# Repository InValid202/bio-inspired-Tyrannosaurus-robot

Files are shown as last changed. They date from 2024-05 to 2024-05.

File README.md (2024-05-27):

# Bio-inspired-Tyrannosaurus-robot
Dinosaur project for RE60429
## Feature
### Robot

Front view

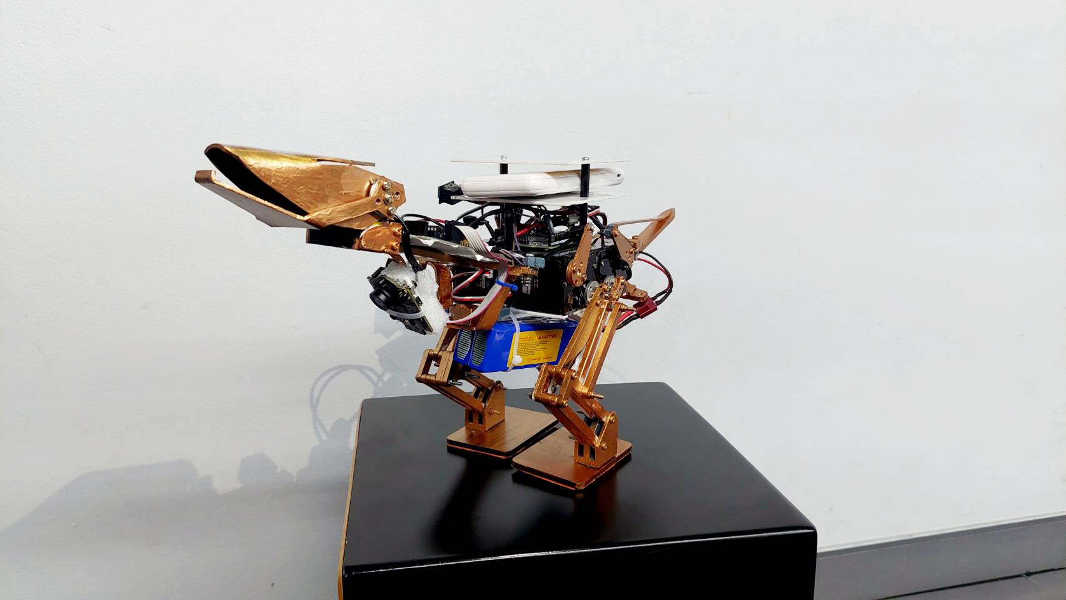
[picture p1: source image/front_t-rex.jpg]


Side view

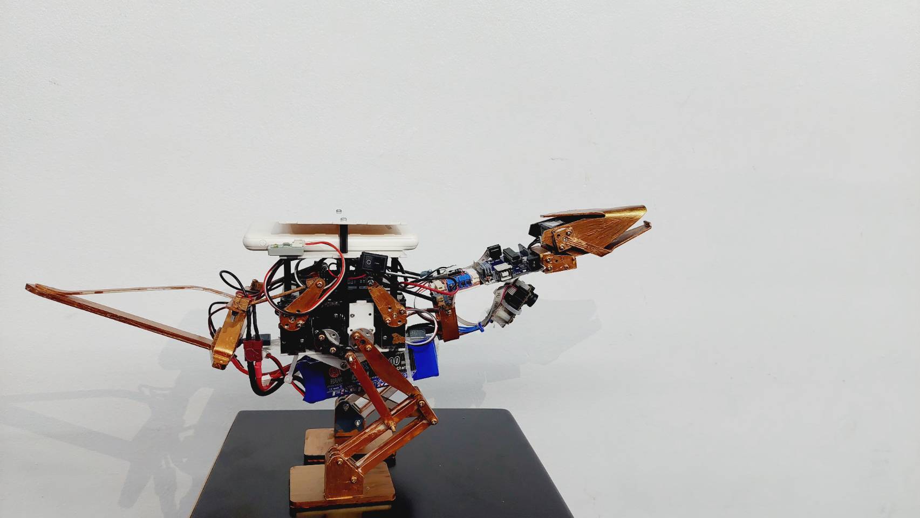
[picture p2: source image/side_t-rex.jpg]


Bird's eye view

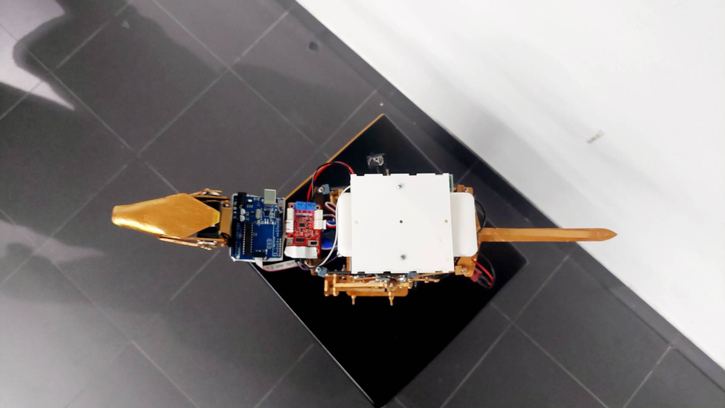
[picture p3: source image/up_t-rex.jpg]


### T-REX's food

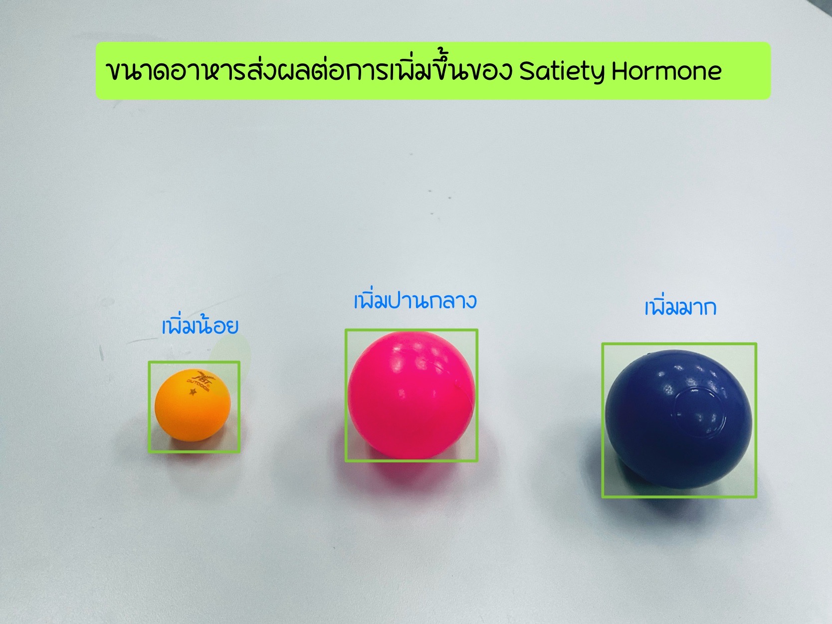
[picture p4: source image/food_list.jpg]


### T-REX's life cycle


## Theory
### CPG with VRNs

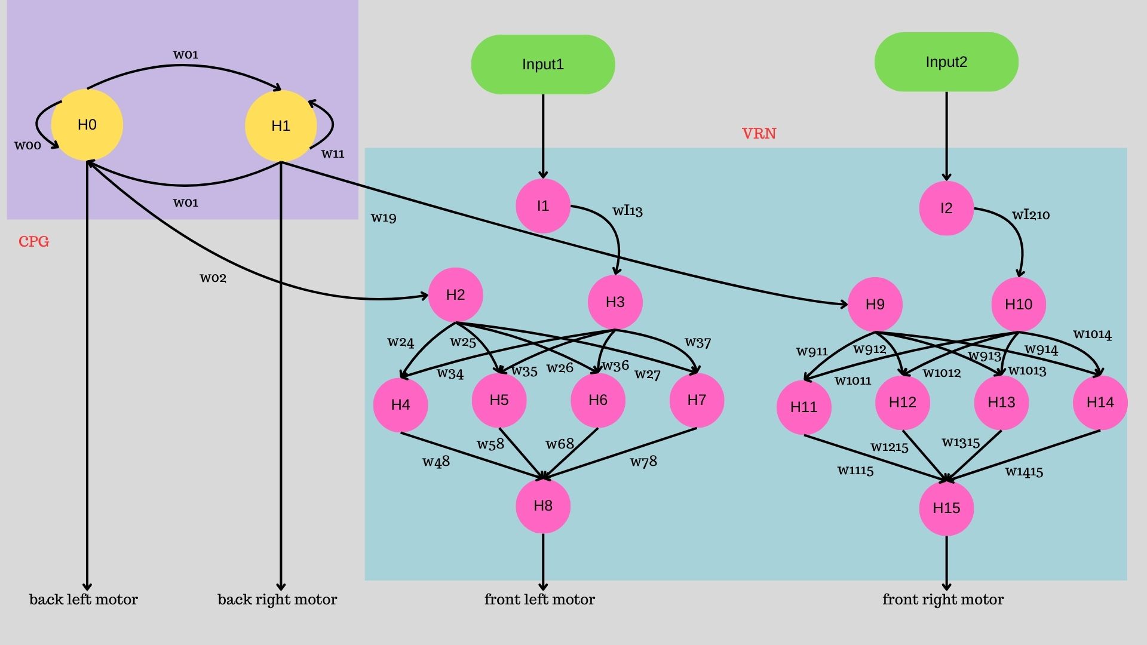
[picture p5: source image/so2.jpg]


spreadsheets for represent CPG and VRNs: [https://docs.google.com/spreadsheets/d/1AZzXm8qZo_j3j6RvV-UtCaSccyqd9fPiu6YYuq5pqpM/edit#gid=0](https://docs.google.com/spreadsheets/d/1AZzXm8qZo_j3j6RvV-UtCaSccyqd9fPiu6YYuq5pqpM/edit?usp=sharing)

as you can see in the spreadsheets you will see a output from both VRNs will always shift a little bit early than original output of SO2 so i assign each VRNs output for each side to the front motor that has responsibility to lift up a leg and assign back motor with output from CPG, this config will generate a pattern of walking by lift up a leg with front motor and follow by stretch leg back with back motor. and other good thing about using VRNs that i can adjust input to modify amplitude of VRNs output. so, i can make my robot turn left and turn right. for example, if i want to turn left i can lower my input1 to make O8 amplitude get lower and will result in lower lifting range but right side still has the same lifting range as before, my robot will start to turn left by it own. 

### Hormone

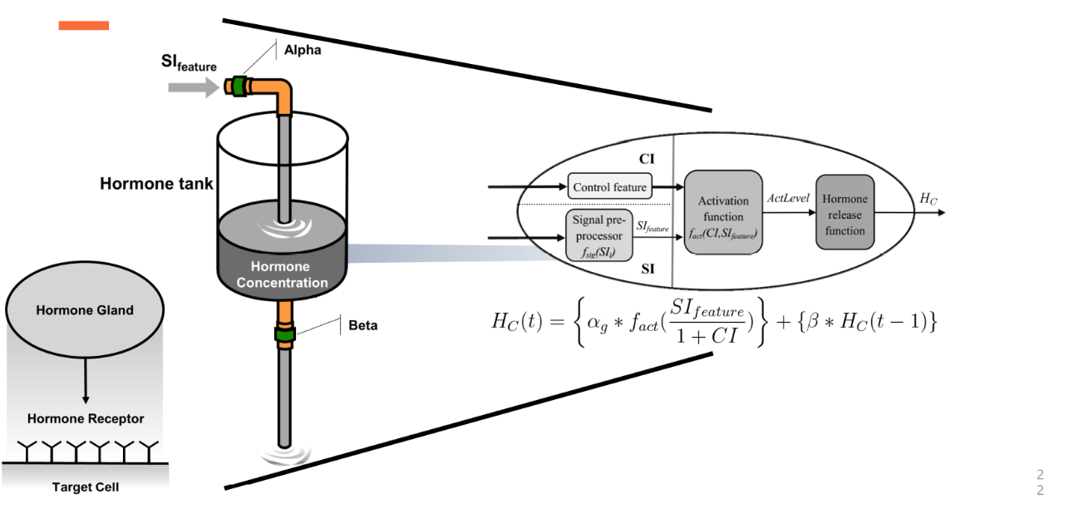
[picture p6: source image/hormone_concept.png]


Example spreadsheets for represent artificial hormones: https://docs.google.com/spreadsheets/d/1hGDivs0pLVSncBLwVF0gHtu8sqr4KoLUj5qkTngY2NQ/edit?usp=sharing

addition paper: [FIBO205_240514_210108.pdf](https://github.com/InValid202/bio-inspired-Tyrannosaurus-robot/files/15449666/FIBO205_240514_210108.pdf)

### System diagram

core concept of this system diagram was to use a Arduino UNO R4 handle all low level control such as drive motor or maybe control a buzzer follow by message from ROS node, and use other ros node handle all high level control such as hormone system calculation and CPG with VRNs

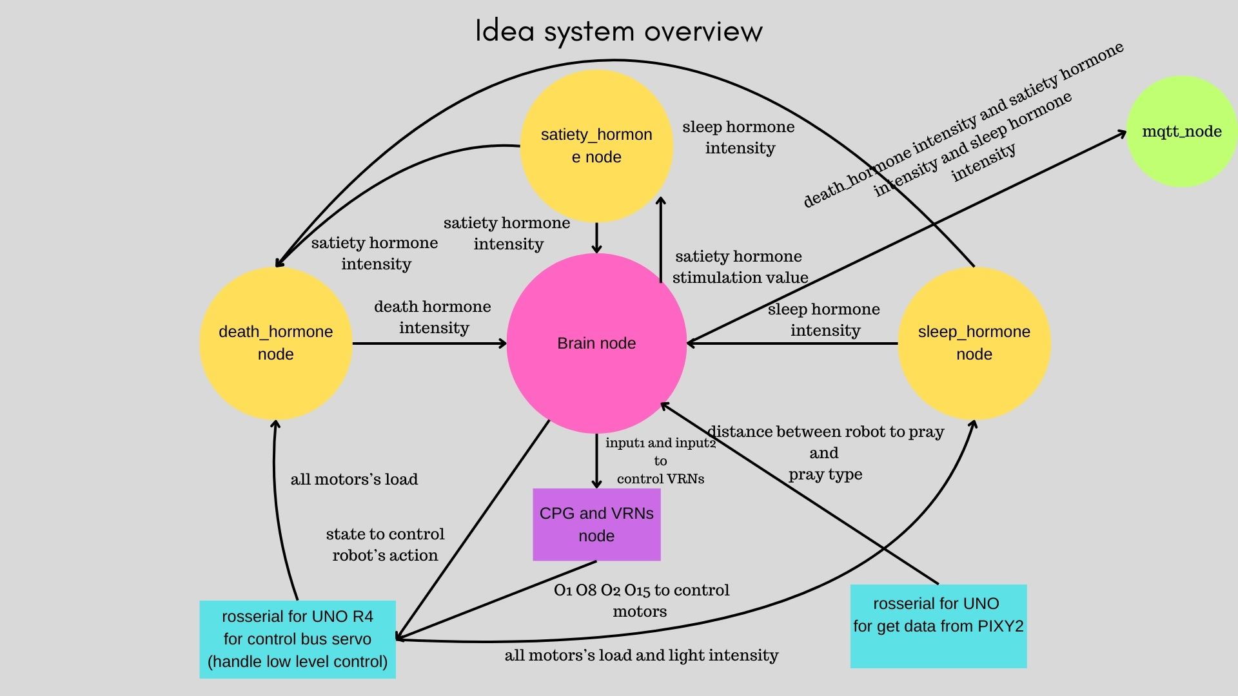
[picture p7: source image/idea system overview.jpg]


After trying to use this system diagram as the core concept for programming, I found that rosserial on the Arduino UNO R4 couldn't handle a message from the ROS CPG node. So, I integrated the following nodes together in the Arduino UNO R4 and ended up with this diagram:

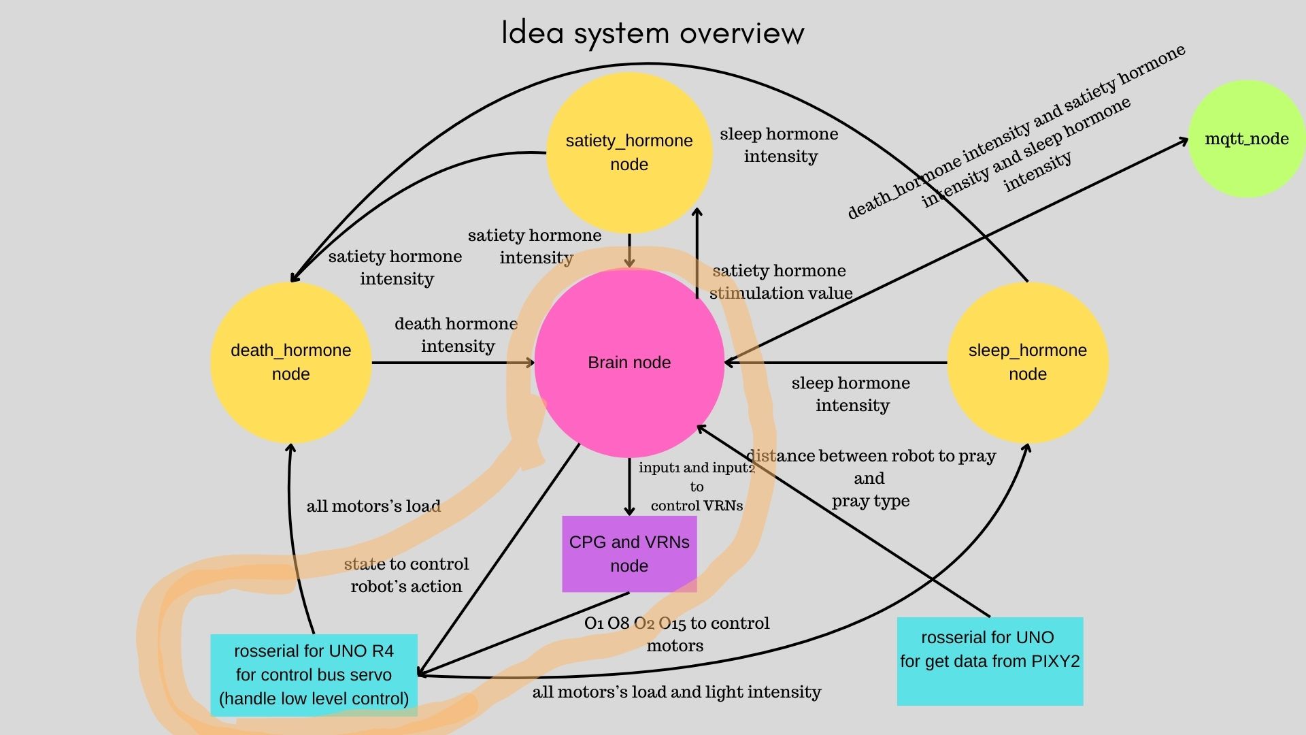
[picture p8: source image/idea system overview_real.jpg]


### Distance calculation Between an Object and a Camera
#### Equation for Finding the Distance Between an Object
and a Camera

𝐷 = 𝑘 / d

Where:

• 𝐷 is the size of the object in the image

• 𝑑 is the distance between the camera and the object

• 𝑘 is a constant that needs to be determined from the actual size of the object

#### Finding the Constant 𝑘
If you know the actual size of the object ( 𝑆 ), you can use the following relationship to
find the constant 𝑘 :

𝑘 = 𝐷 * 𝑑

However, since we do not have the distance ( 𝑑 ) and the diameter in the image ( 𝐷 ), we
need to use the actual size of the object ( 𝑆 ) as a basis to create a general equation.
Suppose you have the actual size of the object 𝑆 = 40 mm.

#### Creating the General Equation
We know that the size of the object in the image ( 𝐷 ) is inversely proportional to the
distance ( 𝑑 ), with a constant 𝑘 that is related to the actual size of the object 𝑆 :

𝑘 = 𝑆 * 𝑑

Thus, the equation becomes:

𝐷 = 𝑘 / d

When 𝑘 = 𝑆 * 𝑑

#### Summary of the Equation

𝐷 = (𝑆 * 𝑑) / 𝑑 = 𝑆

If you know the actual size of the object and the size in the image, you can find the
distance:

𝑑 = 𝑘 / 𝐷

If the constant 𝑘k is not known, you need to know the size of the object in the image
for a given distance or know the focal length of the camera to establish this relationship.

#### Example Usage

Suppose you know the actual size of the object 𝑆=40 mm. and the size of the object in
the image 𝐷 :

If you know that the size of the object in the image at a distance 𝑑 = 10 cm. is 𝐷 = 100
mm. :

1. Find the constant 𝑘 :
𝑘 = 𝐷 * 𝑑 = 100 * 10 = 1000
2. Use the general equation:
𝐷 = 1000 * 𝑑
3. If the size of the object in the image 𝐷D is 50 mm and you want to find 𝑑d :
𝑑 = 1000 / 50 = 20 cm.

This equation can be used when you know the actual size of the object and have
information about the size of the object in the image or the distance in one case to find
the constant 𝑘 first.

## installation

### Hardware:

#### Requirement:

1. Arduino Uno R4 WiFi

2. Arduino Uno R3 

3. Feetech SCS SERVO CONTROLLER

4. Jetson nano

5. Servo scs15

6. pixy2.1
   
7. ZX-02F Light sensor

8. PowerBank 5 V 2A

9. LiPO Battery 3000mAh

10. Rocker switch ON-OFF

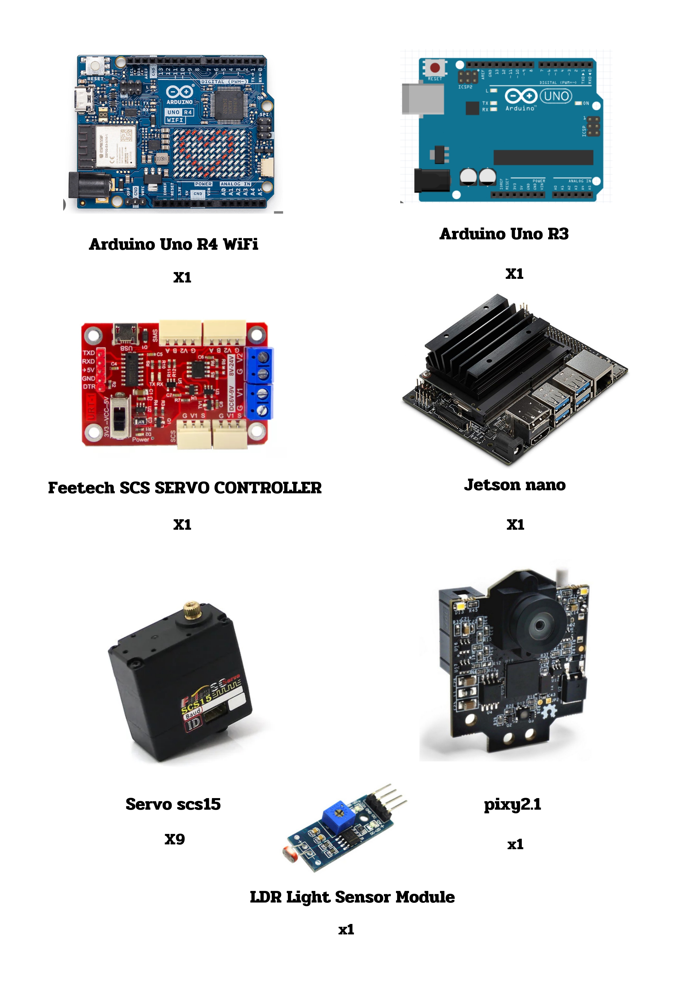
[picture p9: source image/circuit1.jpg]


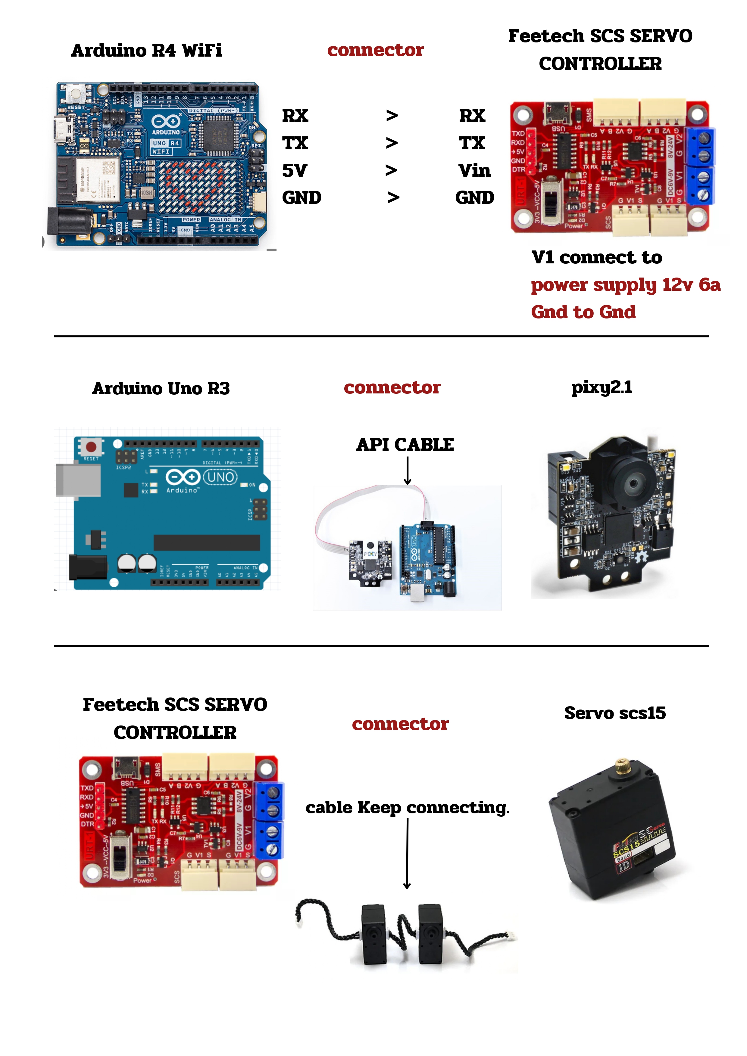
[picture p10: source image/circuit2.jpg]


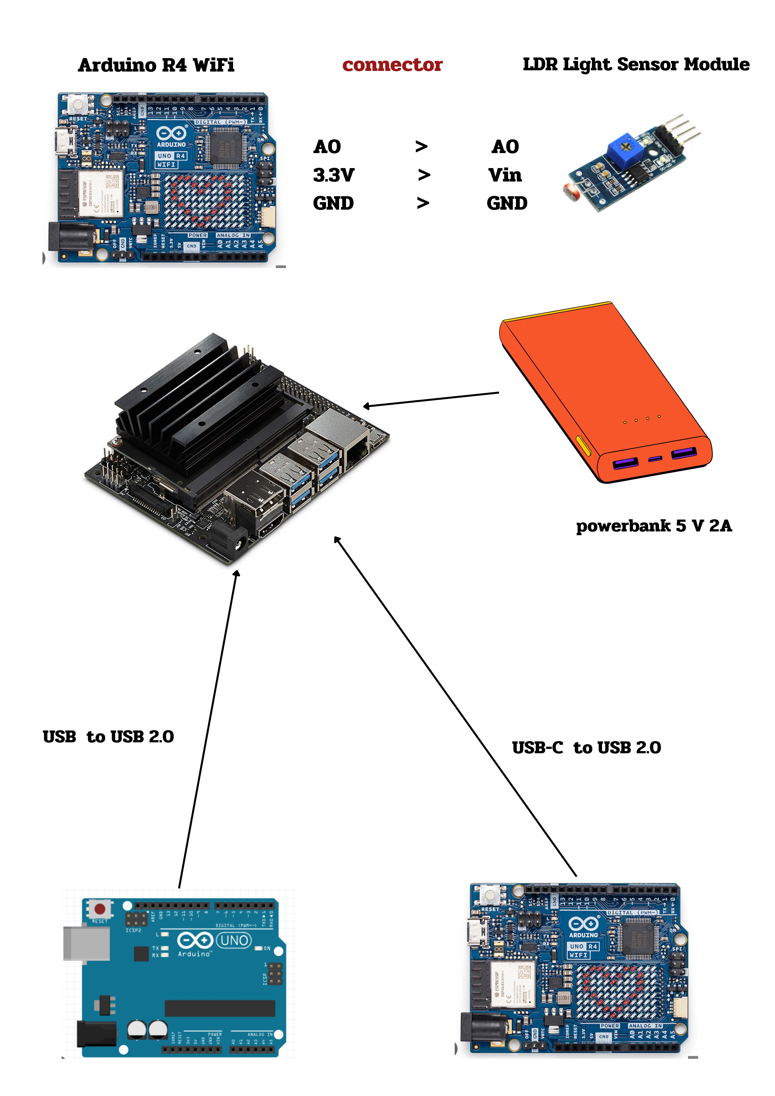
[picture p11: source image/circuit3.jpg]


### software:

#### Requirement:

1. Ubuntu 20.04
2. ROS noetic
3. Arduino IDE
4. Node-RED (Node-RED install tutorial: https://www.arubacloud.com/tutorial/how-to-install-node-red-on-ubuntu-20-04.aspx)

step 1: go to src in your catkin_ws with terminal and run this command in terminal

         git clone https://github.com/InValid202/bio-inspired-Tyrannosaurus-robot.git

step 2: copy both SCServo-master and Pixy2 library file and paste them in libraries folder of Arduino folder

step 3: add the lastest version of Rosserial_Arduino_Library with arduino IDE, follow by this guide: https://support.arduino.cc/hc/en-us/articles/5145457742236-Add-libraries-to-Arduino-IDE

step 4: go to src in your catkin_ws with terminal and run this command in terminal to clone rosserial package for ros

         https://github.com/ros-drivers/rosserial.git

step 5: go back to catkin_ws with terminal and run this command to make package

         catkin_make

step 6: upload code in T-rex.ino to Arduino UNO R4 WIFI

step 7: upload code in pixy_ros.ino to Arduino Uno

step 8: go in to rosserial_arduino package in rosserial that you just clone from step above and go in to nodes folder and edit rospy.init_node

         rospy.init_node("serial_node") --> rospy.init_node("serial_node", anonymous=True)

step 9: launch node-red with this command 

         node-red

step 10: import flows.json that located in node-red_flow folder to Node-RED

step 11: click deploy and use ctrl+shift+d to open dash board

step 12: use this command to start ros master

         roscore

step 13: start both rosserial for both arduino

         rosrun rosserial_arduino serial_node.py _port:=/dev/ttyACM0 _baud:=57600
         rosrun rosserial_arduino serial_node.py _port:=/dev/ttyACM1 _baud:=57600

step 14: launch hormones nodes with this command

         roslaunch t-rex hormone.launch

## Group member

Panchapol Supankhan 6452500091 

Natthachai piyatarathibeth 6452500171 

Paradon chaiyasat 6452500333 

Tumpoom Kanta-in 6452500368 

Terdsak Kanjanawerod 6452500406 

Precha Chuwong 6452500414

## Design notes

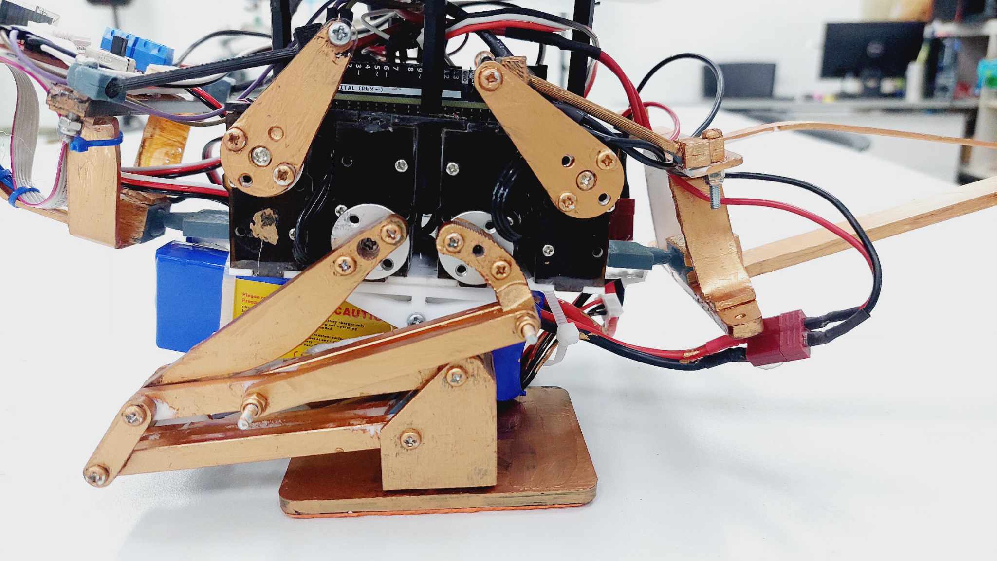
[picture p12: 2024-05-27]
source image/left_side.jpeg

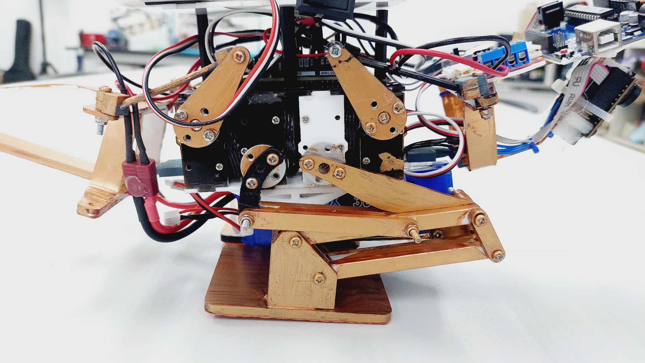
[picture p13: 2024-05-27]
source image/right_side.jpeg

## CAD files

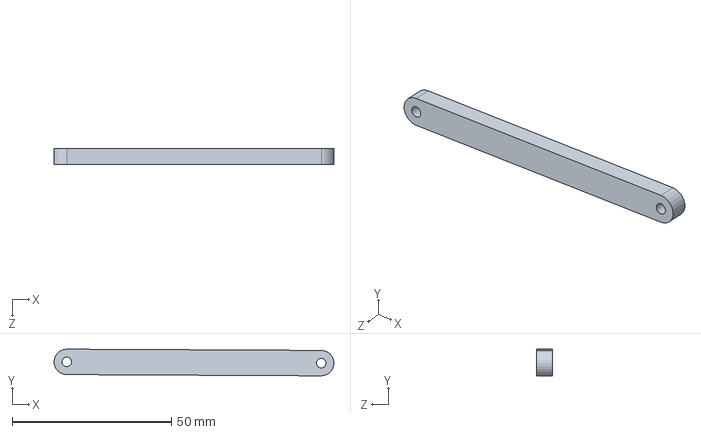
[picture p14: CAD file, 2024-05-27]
CAD/103.SLDPRT
88.0 x 8.40 x 5.00 mm

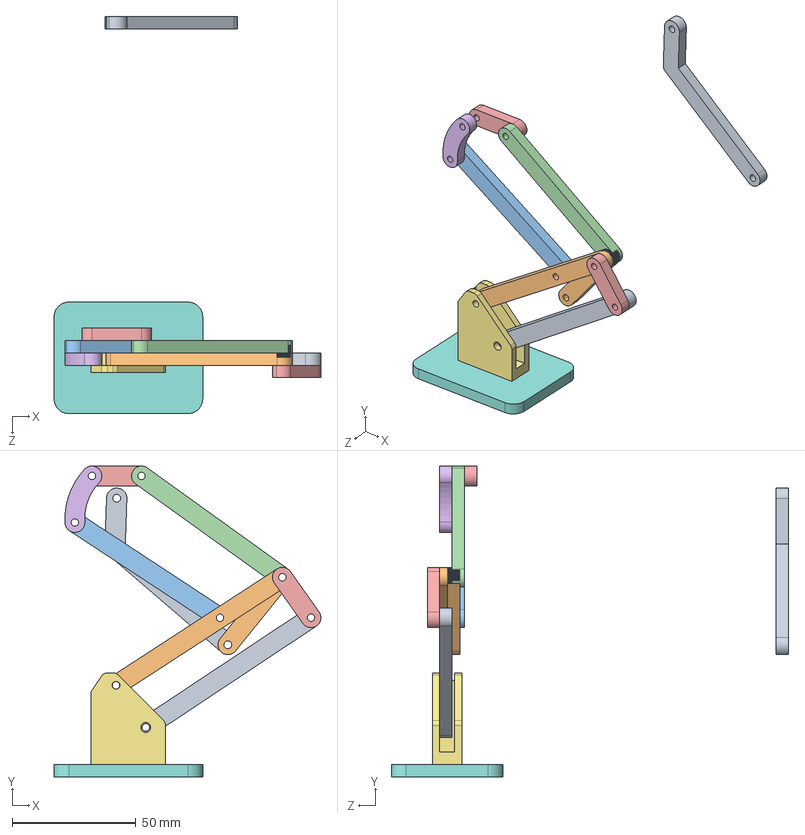
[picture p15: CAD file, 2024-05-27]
CAD/Assem1.STEP
107.7 x 125.4 x 160.2 mm
????
???????

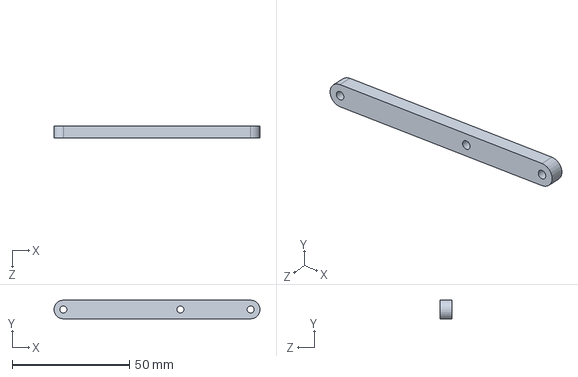
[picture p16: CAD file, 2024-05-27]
CAD/103.1.SLDPRT
88.0 x 8.00 x 5.00 mm

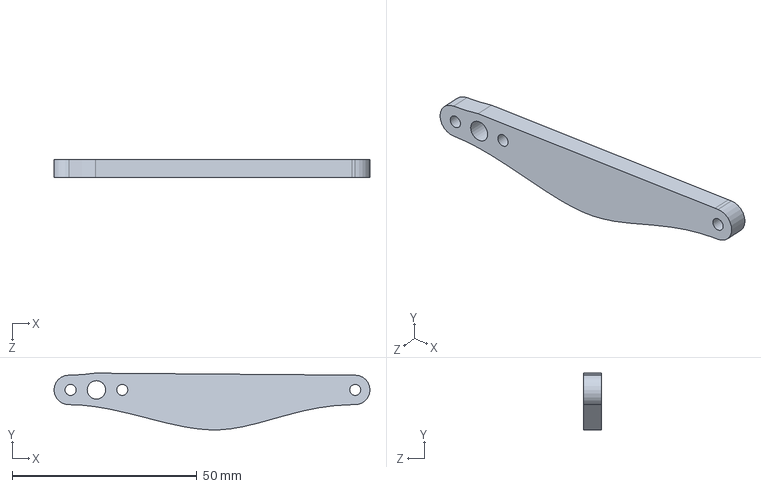
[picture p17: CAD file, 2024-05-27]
CAD/134.SLDPRT
85.6 x 15.4 x 5.01 mm

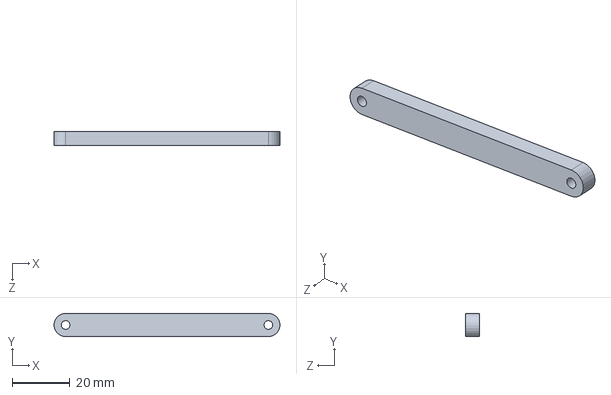
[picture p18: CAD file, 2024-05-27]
CAD/110.SLDPRT
78.0 x 8.00 x 5.00 mm

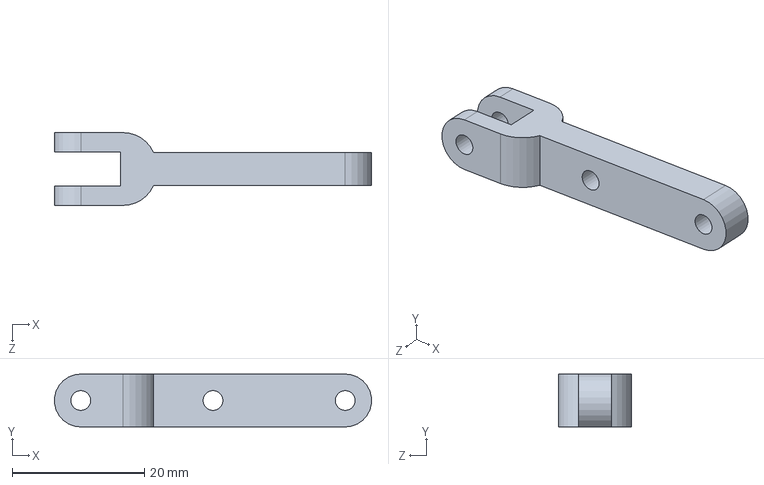
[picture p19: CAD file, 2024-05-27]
CAD/33.SLDPRT
47.9 x 8.00 x 11.0 mm

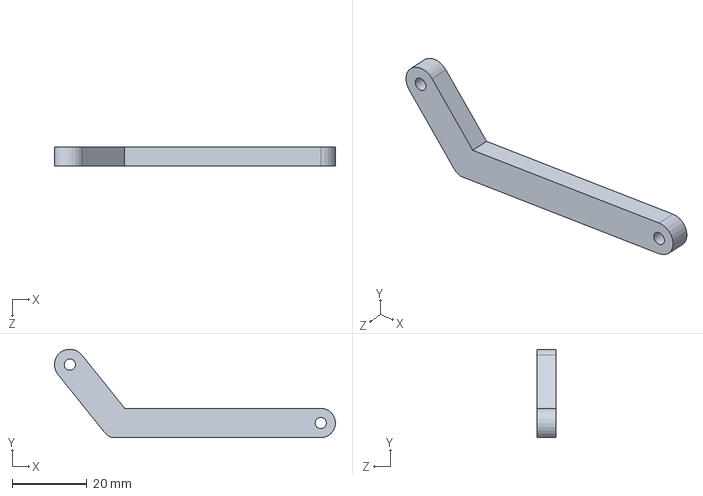
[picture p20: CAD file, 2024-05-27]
CAD/Part2.SLDPRT
75.0 x 23.6 x 5.00 mm

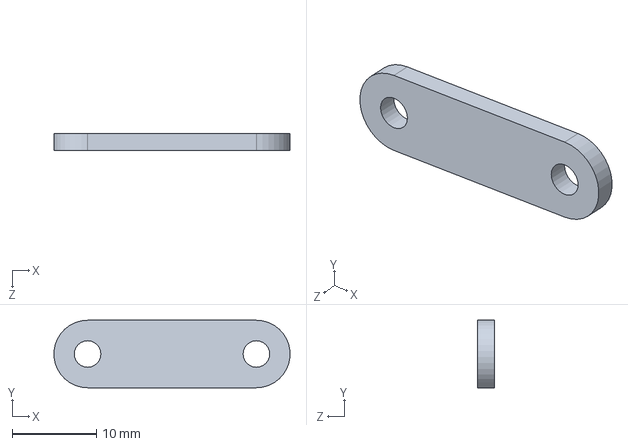
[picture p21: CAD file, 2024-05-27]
CAD/Part1.SLDPRT
28.0 x 8.00 x 2.00 mm

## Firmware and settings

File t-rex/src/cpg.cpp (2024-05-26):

#include "ros/ros.h"
#include "std_msgs/Int16MultiArray.h"
#include "std_msgs/Int16.h"
#include <vector>
#include <cstdlib> // For rand() and srand()
#include <ctime>   // For time()
#include <cmath>
#include <math.h>


//impedance control
float stiffness = 0.05;
float damping = 0.032;


const int to_low_motor2 = 70;
const int to_high_motor2 = 250;

const int to_low_motor3 = 200;
const int to_high_motor3 = 350;

const int to_low_motor9 = 70;
const int to_high_motor9 = 250;
// const int to_high_motor9 = 370;

const int to_low_motor7 = 200;
const int to_high_motor7 = 350;
// const int to_high_motor7 = 500;


int16_t input1 = 1;
int16_t input2 = 1;



// right
int motor1 = 0; 
int motor2 = 0; // front right
int motor3 = 0; // back right
int motor4 = 0;
int motor5 = 0;


int motor6 = 0; // not found 

// left
int motor7 = 0; // back left
int motor8 = 0;
int motor9 = 0; // front left
int motor10 = 0;
int motor11 = 0;
int motor12 = 0;

float interval = 15;

std::vector<int16_t> load_data { 0, 0, 0, 0, 0, 0, 0, 0, 0, 0, 0, 0 };
std::vector<int16_t> speed_data { 0, 0, 0, 0, 0, 0, 0, 0, 0, 0, 0, 0 };
std::vector<int16_t> position_data { 0, 0, 0, 0, 0, 0, 0, 0, 0, 0, 0, 0 };

std::vector<int16_t> motor_command;


int mapf(double val, double in_min, double in_max, double out_min, double out_max) 
{
  return (val - in_min) * (out_max - out_min) / (in_max - in_min) + out_min;
}


void input1_callback(const std_msgs::Int16::ConstPtr& msg)
{
    input1 = msg->data; 	
}


void input2_callback(const std_msgs::Int16::ConstPtr& msg)
{
    input2 = msg->data; 
}



void load_callback(const std_msgs::Int16MultiArray::ConstPtr& msg)
{
    load_data = msg->data;
}



void speed_callback(const std_msgs::Int16MultiArray::ConstPtr& msg)
{

    speed_data = msg->data;
}


void position_callback(const std_msgs::Int16MultiArray::ConstPtr& msg)
{
    position_data = msg->data; 
}


int main(int argc, char **argv)
{


	// Initialize the ROS system and become a node.
	    ros::init(argc, argv, "cpg");
	    ros::NodeHandle nh;
	    
	    // CPG's variable

	    float alpha = 1.03;
	    float phi = M_PI/10;
	    float MI = 0;
	    
	    float B_CPG = 0;
	    	    
	    float w00 = alpha * cos(phi);
  	    float w01 = alpha * sin(phi);
  	    float w10 = -(alpha * (sin(phi)) + MI);
	    float w11 = alpha * cos(phi);
	    	    
	    float c0 = 0.5;
	    float c1 = 0.5;
	    
	    float o0 = tanh(c0);
	    float o1 = tanh(c1);
	    
	    ROS_INFO("first o2: %f", o0);
	    ROS_INFO("first o1: %f", o1);
	    
	    
	    // left VRN's variable
	     
	    float w02 = 1.75;
	    float wi3 = 5;
	    float w24 = 0.5; // main A parameter
	    float w34 = w24;
	    float w25 = -0.5; // main c parameter
	    float w35 = w25;
	    float w26 = w24;
	    float w36 = w25;
	    float w27 = w25;
	    float w37 = w24;
	    float w48 = 0.5;
	    float w58 = 0.5;
	    float w68 = -0.5;
	    float w78 = -0.5;
	    
	    float B_VRN = 1;
	   
	    	    
	    float h2 = 0;
	    float h3 = 0;
	    float h4 = 0;
	    float h5 = 0;
	    float h6 = 0;
	    float h7 = 0;
	    float h8 = 0;
	    
	    float oi1 = tanh(input1);
	    float o2 = tanh(h2);
	    float o3 = tanh(h3);
	    float o4 = tanh(h4);
	    float o5 = tanh(h5);
	    float o6 = tanh(h6);
	    float o7 = tanh(h7);
	    float o8 = tanh(h8);
	    
	    
	    
	    // right VRN's variable
	    
	    float w19 = 1.75;
	    float wi10 = 5;
	    float w911 = w24;
	    float w1011 = w24;
	    float w912 = w25;
	    float w1012 = w25;
	    float w913 = w24;
	    float w1013 = w25;
	    float w914 = w25;
	    float w1014 = w24;
	    float w1115 = 0.5;
	    float w1215 = 0.5;
	    float w1315 = -0.5;
	    float w1415 = -0.5;	    
	    
	    
	    float h9 = 0;
	    float h10 = 0;
	    float h11 = 0;
	    float h12 = 0;
	    float h13 = 0;
	    float h14 = 0;
	    float h15 = 0;
	     
	    float oi2 = tanh(input2);
	    float o9  = tanh(h9);
	    float o10 = tanh(h10);
	    float o11 = tanh(h11);
	    float o12 = tanh(h12);
	    float o13 = tanh(h13);
	    float o14 = tanh(h14);
	    float o15 = tanh(h15);  
	    
	    // Create a publisher object.
	    ros::Publisher pub = nh.advertise<std_msgs::Int16MultiArray>("cpg", 12);
	    
	    
	    // Create a subscriber object.
	    
	    ros::Subscriber sub1 = nh.subscribe("input_1", 1000, input1_callback);
	    ros::Subscriber sub2 = nh.subscribe("input_2", 1000, input2_callback);
	    
	    ros::Subscriber sub_load = nh.subscribe("arduino_Load", 1000, load_callback);
	    ros::Subscriber sub_speed = nh.subscribe("arduino_Position", 1000, speed_callback);
	    ros::Subscriber sub_position = nh.subscribe("arduino_Speed", 1000, position_callback);
	    


	    // Loop at 1Hz until the node is shut down.
	    ros::Rate rate(interval);
	    while (ros::ok())
	    {
	    	// CPG SO2 equation
	    	c0 = w10 * o1 + w00 * o0;
	    	c1 = w01 * o0 + w11 * o1;
	    	
	    	// ROS_INFO("c0: %f", c0);
	    	// ROS_INFO("C1: %f", c1);
	    
	        // left VRNs equation
	        
	    	h2 = o0 * w02; 
	    	h3 = oi1 * wi3;
	    	h4 = o2 * w24 + o3 * w34 + B_VRN; 
	    	h5 = o2 * w25 + o3 * w35 + B_VRN;
	    	h6 = o2 * w26 + o3 * w36 + B_VRN;
	    	h7 = o2 * w27 + o3 * w37 + B_VRN;
	    	h8 = o4 * w48 + o5 * w58 + o6 * w68 + o7 * w78;
	    	
	    	// right VRNs equation
	    	 
	    	h9 = o1*w19;
	    	h10 =oi2 * wi10;
	    	h11 = o9 * w911 + o10 * w1011 + B_VRN;
	    	h12 = o9 * w912 + o10 * w1012 + B_VRN;
	    	h13 = o9 * w913 + o10 * w1013 + B_VRN;
	    	h14 = o9 * w914 + o10 * w1014 + B_VRN;
	    	h15 = o11 * w1115 + o12 * w1215 + o13 * w1315 + o14 * w1415; 
	    	
	    	// CPG output
	    	
	    	o0 = tanh(c0);
	    	o1 = tanh(c1);
	    
	 	
	    	// left VRNs output
	    	
	    	oi1 = tanh(input1);
	    	o2 = tanh(h2);
	    	o3 = tanh(h3);
	    	o4 = tanh(h4);
	    	o5 = tanh(h5);
	    	o6 = tanh(h6);
	    	o7 = tanh(h7);
	    	o8 = tanh(h8);
	    	
		// right VRNS output
		
		oi2 = tanh(input2);
		o9  = tanh(h9);
		o10 = tanh(h10);
		o11 = tanh(h11);
		o12 = tanh(h12);
		o13 = tanh(h13);
		o14 = tanh(h14);
		o15 = tanh(h15); 
		

	    	ROS_INFO("o0 : %f", o0);
	    	ROS_INFO("o1 : %f", o1);
	    	
	    	ROS_INFO("o8 : %f", o8);
	    	ROS_INFO("o15: %f", o15);
	    	
	    	ROS_INFO("next");
	    	
	    	
	    	if (o0 < -0.3353811311) 
	    	{
  			o0 = -0.3353811311;
		}  
		else if (o0 > 0.3358224348)
		{
			o0 = 0.3358224348;
		}
		
		
		if (o1 < -0.3352863688) 
	    	{
  			o1 = -0.3352863688;
		} 
		else if (o1 > 0.3384303953)
		{
			o1 = 0.3384303953;
		}
		
		
		if (o8 < -0.3031119357) 
	    	{
  			o8 = -0.3031119357;
		}  
		else if (o8 > 0.3033082662)
		{
			o8 = 0.3033082662;
		}
		
		
	    	if (o15 < -0.3353811311) 
	    	{
  			o15 = -0.3353811311;
		}  
		else if (o15 > 0.3358224348)
		{
			o15 = 0.3358224348;
		}
		
		ROS_INFO("checkpoint start");
		
		motor_command.push_back(0); // 1
		motor_command.push_back(1023 - mapf(o15, -0.3031119357, 0.3033082662, to_low_motor2, to_high_motor2)); // 2
		motor_command.push_back(1023 - mapf(o1, -0.3352863688, 0.3384303953, to_low_motor3, to_high_motor3)); // 3
		motor_command.push_back(0); // 4
		motor_command.push_back(0); // 5
		motor_command.push_back(0); // 6
		motor_command.push_back(mapf(o0, -0.3353811311, 0.3358224348, to_low_motor7, to_high_motor7)); // 7 
		motor_command.push_back(0); // 8
		motor_command.push_back(mapf(o8, -0.3031119357, 0.3033082662, to_low_motor9, to_high_motor9)); // 9
		motor_command.push_back(0); // 10
		motor_command.push_back(0); // 11
		motor_command.push_back(0); // 12
		
		
	  	// motor2 = 1023 - mapf(o15, -0.3031119357, 0.3033082662, to_low_motor2, to_high_motor2);
	  	// motor3 = 1023 - mapf(o1, -0.3352863688, 0.3384303953, to_low_motor3, to_high_motor3);
	  	
	  	
	  	// motor7 = mapf(o0, -0.3353811311, 0.3358224348, to_low_motor7, to_high_motor7);
	  	// motor9 = mapf(o8, -0.3031119357, 0.3033082662, to_low_motor9, to_high_motor9);
	  	
	    	

	      	// Create and fill in the message.
		std_msgs::Int16MultiArray msg;

		// Define layout if needed (optional).
		msg.layout.dim.push_back(std_msgs::MultiArrayDimension());
		msg.layout.dim[0].size = 12;
		msg.layout.dim[0].stride = 1;
		msg.layout.dim[0].label = "motor_output";
		
	    	for (int i = 0; i < 12; i++) 
	    	{
	    		
  			//float torque = (stiffness*(motor_command[i] - position_data[i])) + (damping * (0.0- speed_data[i]));
  			
  			// msg.data.push_back(motor_command[i]+ torque);
  			msg.data.push_back(motor_command[i]);
		} 
	  	
	  	motor_command.clear();
	  	
		// Publish the message.
		pub.publish(msg);

		// Wait until it's time for another iteration.
		rate.sleep();
    }
}

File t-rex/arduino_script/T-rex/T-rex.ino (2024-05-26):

#include <SCServo.h>
#include <ros.h>
#include <std_msgs/Int16MultiArray.h>
#include <std_msgs/Float32MultiArray.h>
#include <std_msgs/Int16.h>
#include <std_msgs/Float32.h>

#define NUM_SERVOS 9

unsigned long last_time = 0;
unsigned long last_time_food = 0;
 
const long INTERVAL_move= 2; // Interval for publishing load data in milliseconds
const long INTERVAL_life = 200; 

int16_t distance_from_pray = 1000;
float pray = 0;
float pray_target = 0;

int16_t food_count = 0;
int16_t motor_speed = 1500;

int16_t state = 1;

float satiety_Hormone = 0.0;
float sleep_Hormone = 0.0;
float death_Hormone = 0.0;

float death_bar = 0;
float sleep_bar = 0;

int16_t camera_array[8]; 

// 1 = normal walking mode
// 2 = hunting mode
// 3 = sleep mode
// 4 = death mode
// 5 = eating mode
// 6 = wake up mode

const int to_low_motor2 = 0; // right front leg 
const int to_high_motor2 = 100; 

const int to_low_motor3 = 0; // right back leg 
const int to_high_motor3 = 180;

const int to_low_motor6 = 0; // left front leg 
const int to_high_motor6 = 100;

const int to_low_motor7 = 0; // left back leg 
const int to_high_motor7 = 180;

const int to_low_motor5 = 220; // left_head
const int to_high_motor5 = 350;

const int to_low_motor1 = 220; // right_head
const int to_high_motor1 = 350;

const int to_low_motor8 = 200; // left_tail 
const int to_high_motor8 = 270;

const int to_low_motor4 = 200; // right_tail
const int to_high_motor4 = 270;

int16_t input1 = 1;
int16_t input2 = 1;

// right
int motor1 = 0; 
int motor2 = 0; // front right
int motor3 = 0; // back right
int motor4 = 0;
int motor5 = 0;

// int motor6 = 0; // not found 

// left
int motor7 = 0; // back left
int motor8 = 0;
int motor6 = 0; // front left
int motor10 = 0;
int motor11 = 0;
int motor12 = 0;

float alpha = 1.03;
float phi = M_PI/10;
float MI = 0.05;
      
float B_CPG = 0;
            
float w00 = alpha * cos(phi);
float w01 = alpha * sin(phi+MI);
float w10 = alpha * (-sin(phi+MI));
float w11 = alpha * cos(phi);
            
float c0 = 0.5;
float c1 = 0.5;

float o0 = tanh(c0);
float o1 = tanh(c1);
        
// left VRN's variable
       
float w02 = 1.75;
float wi3 = 5;
float w24 = 0.5; // main A parameter
float w34 = w24;
float w25 = -0.5; // main c parameter
float w35 = w25;
float w26 = w24;
float w36 = w25;
float w27 = w25;
float w37 = w24;
float w48 = 0.5;
float w58 = 0.5;
float w68 = -0.5;
float w78 = -0.5;
   
float B_VRN = 1;
          
float h2 = 0;
float h3 = 0;
float h4 = 0;
float h5 = 0;
float h6 = 0;
float h7 = 0;
float h8 = 0;
      
float oi1 = tanh(input1);
float o2 = tanh(h2);
float o3 = tanh(h3);
float o4 = tanh(h4);
float o5 = tanh(h5);
float o6 = tanh(h6);
float o7 = tanh(h7);
float o8 = tanh(h8);
        
// right VRN's variable
      
float w19 = 1.75;
float wi10 = 5;
float w911 = w24;
float w1011 = w24;
float w912 = w25;
float w1012 = w25;
float w913 = w24;
float w1013 = w25;
float w914 = w25;
float w1014 = w24;
float w1115 = 0.5;
float w1215 = 0.5;
float w1315 = -0.5;
float w1415 = -0.5;     
      
      
float h9 = 0;
float h10 = 0;
float h11 = 0;
float h12 = 0;
float h13 = 0;
float h14 = 0;
float h15 = 0;
       
float oi2 = tanh(input2);
float o9  = tanh(h9);
float o10 = tanh(h10);
float o11 = tanh(h11);
float o12 = tanh(h12);
float o13 = tanh(h13);
float o14 = tanh(h14);
float o15 = tanh(h15);  


SCSCL sc;
ros::NodeHandle nh;


std_msgs::Int16MultiArray load_msg;
//std_msgs::Float32 mi;
//std_msgs::Float32 motor_speed;
// std_msgs::Int16MultiArray position_msg;
// std_msgs::Int16MultiArray speed_msg;

std_msgs::Int16 light_msg;
std_msgs::Float32 food_msg;       
                  
std_msgs::Int16 death_bar_msg;
std_msgs::Int16 sleep_bar_msg;  

// Array to store servo load data

int16_t load_data[NUM_SERVOS];
int16_t speed_data[NUM_SERVOS];
int16_t position_data[NUM_SERVOS];

int sensorPin = A0;
int sensorValue = 0;


// Function prototypes
int mapf(double , double , double , double , double );

void inputCallback(const std_msgs::Int16 &msg);

void camera_callback(const std_msgs::Int16MultiArray &msg);

void satiety_callback(const std_msgs::Float32 &msg);

void sleep_callback(const std_msgs::Float32 &msg);

void death_callback(const std_msgs::Float32 &msg);
 
void get_feedback_pub();


// feedback publisher 
ros::Publisher load_pub("arduino_Load", &load_msg);
ros::Publisher food_pub("food_stimulate", &food_msg); 

// publish status
ros::Publisher death_bar_pub("death_bar", &death_bar_msg); 
ros::Publisher sleep_bar_pub("sleep_bar", &sleep_bar_msg); 

// sensor publisher
ros::Publisher Light("Light", &light_msg);


// subscriber for state and turn right and left
ros::Subscriber<std_msgs::Int16> sub_input("/input", inputCallback); 
ros::Subscriber<std_msgs::Int16MultiArray> sub_camera("/pixy", camera_callback); 
ros::Subscriber<std_msgs::Float32> sub_satiety("/satiety_hormone", satiety_callback); 
ros::Subscriber<std_msgs::Float32> sub_sleep("/sleep_hormone", sleep_callback); 
ros::Subscriber<std_msgs::Float32> sub_death("/death_hormone", death_callback); 

void setup() {
  Serial1.begin(1000000);
  // Serial.begin(9600); // for test
  // Serial.begin(1000000);
  sc.pSerial = &Serial1;
  
  
  nh.initNode();
  nh.getHardware()->setBaud(57600);
  
  nh.subscribe(sub_input);
  nh.subscribe(sub_camera);
  nh.subscribe(sub_satiety);
  nh.subscribe(sub_sleep);
  nh.subscribe(sub_death);

  nh.advertise(load_pub);
  nh.advertise(food_pub);
  
  nh.advertise(death_bar_pub);
  nh.advertise(sleep_bar_pub);
  
  nh.advertise(Light);
}
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
